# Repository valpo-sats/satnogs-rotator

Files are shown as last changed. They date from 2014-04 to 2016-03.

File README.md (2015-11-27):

# SatNOGS Rotator

Hardware for SatNOGS Rotator. This repository includes all needed source files for 3D printed (and other) parts of SatNOGS Rotator.

## Documentation

More information can be found in our [documentation](http://satnogs.org/documentation/hardware/), or our [wiki](https://wiki.satnogs.org).

## Repository policy
SatNOGS hardware repositories only track source design files. All needed derivative files (e.g. stl, grb etc) for production are created per release, packaged in an archive and uploaded linked to a  [release](https://github.com/satnogs/satnogs-rotator/releases).

Each major release (x.0.0) is branched out of master. Subsequent fixes (minor or not) are commited on those branches and tagged accordingly.

Master branch is most times under active development, so expect things to break. For production ready and previous releases source files check tags and branches.

## License

&copy; 2014-2015 [Libre Space Foundation](http://librespacefoundation.org).

Licensed under the [CERN OHLv1.2](LICENSE).

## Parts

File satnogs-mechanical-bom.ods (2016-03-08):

Part | Description | Distributor | Qty | Price Per Unit Small QNT (euro) | Total Price | Printing Time (min) | Price Per Unit Large QNT (euro) | Total price | Comments
axis_side.stl | Axis side, 3D printed | - | 2 | 0.8 | 1.6 | 110 | 0.8 | 1.6
axis_side_sensor_holder.stl | Axis side with homing sensor, 3D printed | - | 2 | 0.8 | 1.6 | 128 | 0.8 | 1.6
ball_bearing_housing.stl | Ball bearing housing, 3D printed | - | 4 | 0.8 | 3.2 | 46 | 0.8 | 3.2
axis_spacer.stl | Axis spacer, 3D printed | - | 2 | 0.8 | 1.6 | 15 | 0.8 | 1.6
axis_spacer_collar.stl | Axis spacer collar, 3D printed | - | 2 | 0.8 | 1.6 | 26 | 0.8 | 1.6
axis_gear.stl | Axis gear (Worm wheel), 3D printed | - | 2 | 0.8 | 1.6 | 172 | 0.8 | 1.6
homing_ring.stl | Homing ring, 3D printed | - | 2 | 0.8 | 1.6 | 25 | 0.8 | 1.6
worm_gear.stl | Worm gear, 3D printed | - | 2 | 0.8 | 1.6 | 105 | 0.8 | 1.6
worm_mount.stl | Worm mount, 3D printed | - | 2 | 0.8 | 1.6 | 84 | 0.8 | 1.6 | Printing time is for worm_mount and worm_mount_mirror
worm_mount_mirror.stl | Worm mount mirror, 3D printed | - | 2 | 0.8 | 1.6 | 84 | 0.8 | 1.6
motor_mount_flange.stl | DC Motor mount flange, 3D printed | - | 2 | 0.8 | 1.6 | 21 | 0.8 | 1.6
motor_mount.fcstd | Motor mount | [2] (http://grobotronics.com/stepper-motor-mount-with-hardware.html) | 2 | 4.8 | 9.6 | - | 2.75 | 5.5
encoder_holder.stl | Encoder holder, 3D printed | - | 2 | 0.8 | 1.6 | 81 | 0.8 | 1.6 | Printing time is for 2 encoder_holder and 2 M3_TSlot20_nut
t_slot20_102.fcstd | T slot 20x20 L102 | [1] (http://www.motedis.com/shop/) | 18 | 0.51 | 9.18 | - | 0.3 | 5.4
t_slot20_160.fcstd | T slot 20x20 L160 | [1] (http://www.motedis.com/shop/) | 8 | 0.8 | 6.4 | - | 0.47 | 3.76
axis_pipe_40mm.fcstd | Aluminum pipe Φ40 L1m | - | 2 | 5 | 10 | - | 3 | 6
M3_TSlot20_nut.stl | M3 nut adapter for t slot, to mount encoder Holder, 3D printed | - | 2 | 0.8 | 1.6 | 81 | 0.8 | 1.6
e_box_pcb_mount.stl | PCB mount | - | 1 | 0.8 | 0.8 | 2 | 0.8 | 0.8
lower_bottom.pdf | Part for weather proof box, 1st sheet | - | 1 | 2 | 2 | - | 1.6 | 1.6
lower_side_axis_A.pdf | Part for weather proof box, 1st sheet | - | 1 | 2 | 2 | - | 1.6 | 1.6
lower_side_axis_B.pdf | Part for weather proof box, 2nd sheet | - | 1 | 2 | 2 | - | 1.6 | 1.6
lower_side_axis_x2.pdf | Part for weather proof box, 2nd sheet | - | 2 | 2 | 4 | - | 1.6 | 3.2
upper_side_axis_A.pdf | Part for weather proof box, 3rd sheet | - | 1 | 2 | 2 | - | 1.6 | 1.6
upper_side_axis_B.pdf | Part for weather proof box, 3rd sheet | - | 1 | 2 | 2 | - | 1.6 | 1.6
upper_side_axis_x2.pdf | Part for weather proof box, 4th sheet | - | 2 | 2 | 4 | - | 1.6 | 3.2
upper_top.pdf | Part for weather proof box, 4th sheet | - | 1 | 2 | 2 | - | 1.6 | 1.6
rain_cover_box.stl | Part for weather proof box, 3D printed | - | 2 | 0.8 | 1.6 |  | 0.8 | 1.6
rain_cover_tube.stl | Part for weather proof box, 3D printed | - | 2 | 0.8 | 1.6 |  | 0.8 | 1.6
rain_cover_positioning_pattern.pdf | Pattern to place in the box the Rain_cover_box parts | - | 1 | 0 | 0 | - | 0 | 0
Hidden Corner Connection slot 6 | for t slots | [1] (http://www.motedis.com/shop/) | 44 | 1.4 | 61.6 | - | 0.75 | 33
M5 Threaded Rod | for axis of worm gear, 2xL90mm | - | 2 | 1 | 2 | - | 1 | 2
M5 Hex Nuts | for axis of worm gear | - | 6 | 0.02 | 0.12 | - | 0.02 | 0.12
M5 Washers | for axis of worm gear, OD:10mm | - | 6 | 0.012 | 0.072 | - | 0.012 | 0.072
M4 Nuts slot 6 | for t slots, electronics box and cover box | [1] (http://www.motedis.com/shop/) | 37 | 0.4 | 14.8 | - | 0.18 | 6.66
M4 Head Cap Screw L10 | for t slots, electronics box and cover box | - | 32 | 0.04 | 1.28 | - | 0.04 | 1.28
M4 Head Cap Screw L20 | for ball bearing housing and motor mount | - | 20 | 0.06 | 1.2 | - | 0.06 | 1.2
M4 Hex Nuts | for ball bearing housing and worm gear | - | 20 | 0.014 | 0.28 | - | 0.014 | 0.28
M4 Washers | general, OD:10mm | - | 24 | 0.012 | 0.288 | - | 0.012 | 0.288
M3 Hex Nuts | general | - | 32 | 0.012 | 0.384 | - | 0.012 | 0.384
M3 Washers | general, OD: 8mm | - | 26 | 0.012 | 0.312 | - | 0.012 | 0.312
M3 Set Screw L10 | for axis spacer collar | - | 12 | 0.04 | 0.48 | - | 0.04 | 0.48
M3 Head Cap Screw L6 | for stepper motor, DC motor mount flange ,Encoder holder and electronics box | - | 20 | 0.03 | 0.6 | - | 0.03 | 0.6
M3 Head Cap Screw L12 | for homing sensor holder and DC motor mount | - | 10 | 0.03 | 0.3 | - | 0.03 | 0.3
M3 Head Cap Screw L25 | for homing ring | - | 2 | 0.05 | 0.1 | - | 0.05 | 0.1
M2 Thread-Forming Screw L6 | for encoder holder | - | 2 | 0.05 | 0.1 | - | 0.05 | 0.1
Ball Bearing 6008ZZ | for main axis | - | 4 | 5 | 20 | - | 2 | 8
Ball Bearing 625ZZ | for worm gear axis | - | 4 | 0.8 | 3.2 | - | 0.45 | 1.8
Timing Pulley GT2, 6mm Belt, 20 Tooth, 6mm Bore |  | [2] (http://grobotronics.com/aluminum-gt2-timing-pulley-6mm-belt-20-tooth-5mm-bore.html) | 2 | 4 | 8 | - | 2.27 | 4.54 | For DC motor 6mm Bore
Timing Pulley GT2, 6mm Belt, 36 Tooth, 5mm Bore |  | [2] (http://grobotronics.com/aluminum-gt2-timing-pulley-6mm-belt-36-tooth-5mm-bore.html) | 2 | 6 | 12 | - | 3.4 | 6.8
Timing Belt GT2, 158mm, Wide 6mm | for both axis | [2] (http://grobotronics.com/timing-belt-gt2-158mm.html) | 2 | 1.5 | 3 | - | 0.85 | 1.7
 |  |  |  | Total | 211.696 |  |  | 133.076

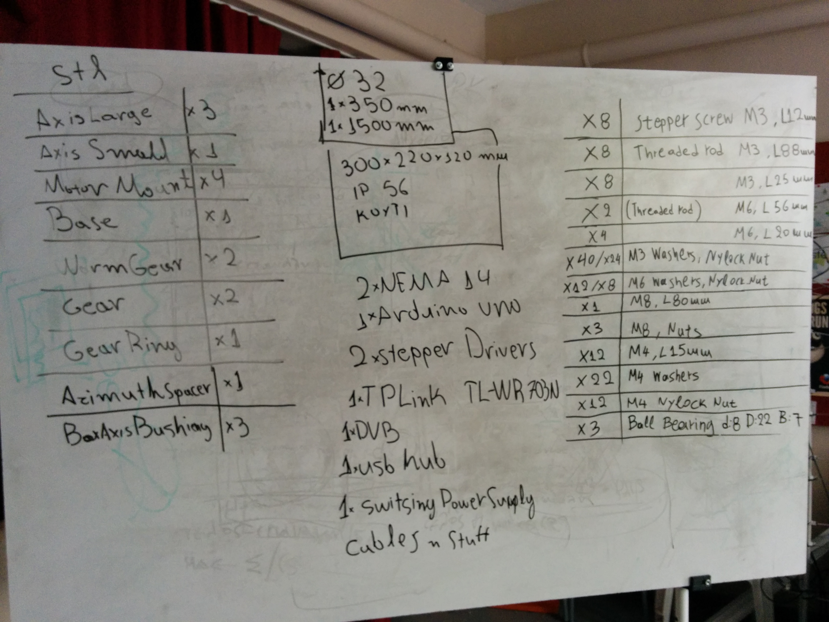
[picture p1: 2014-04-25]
doc/Parts.jpg

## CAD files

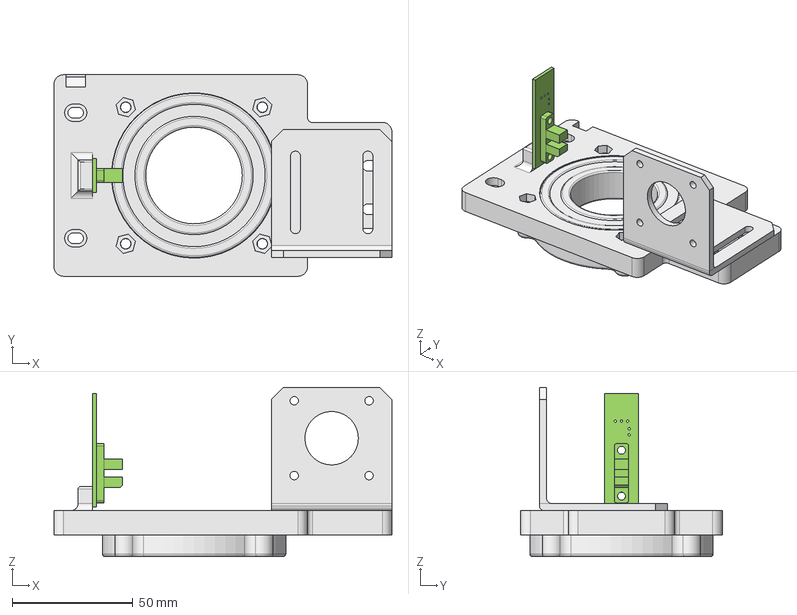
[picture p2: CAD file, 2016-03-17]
assemblies/axis_side_sensor_holder_assembly.fcstd
140.0 x 83.5 x 70.0 mm
axis_side_sensor_holder_01
satnogs_endstop_01
motor_mount_01
ball_bearing_housing_01
ball_bearing_6008ZZ_01

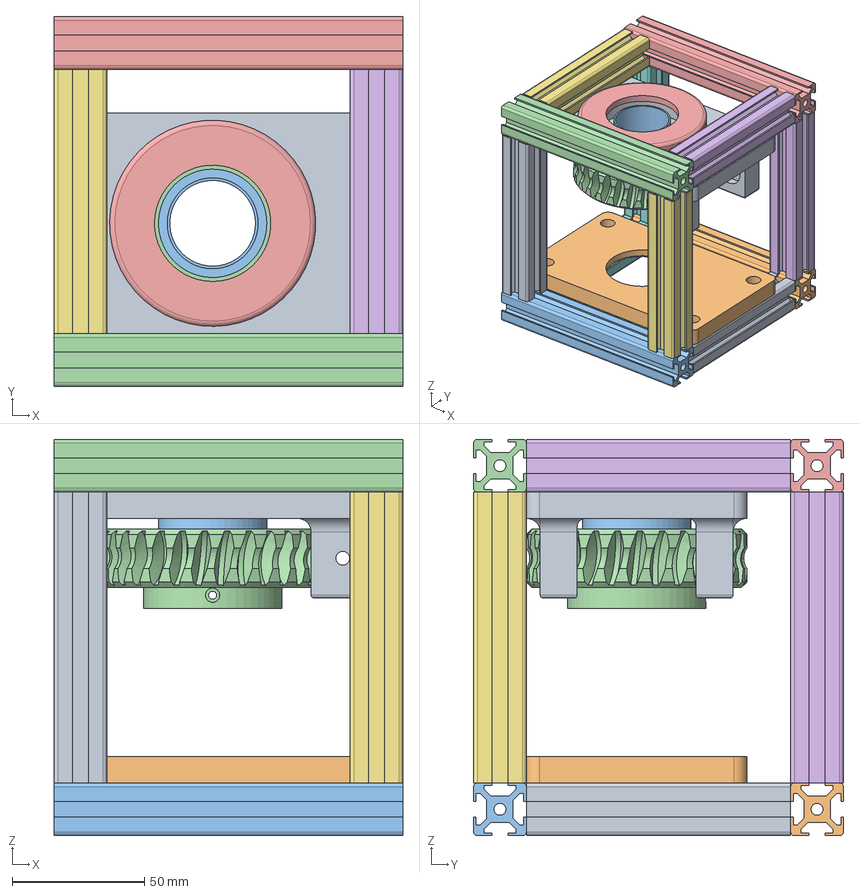
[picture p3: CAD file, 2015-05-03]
src/Assembly.fcstd
132.0 x 140.0 x 150.0 mm
axis_side_worm_mount_import01
axis_side_motor_mount_import01
axis_spacer_import01
axis_gear_import01
ball_bearing_housing_import01
t_slot20_100_import01
t_slot20_100_import02
t_slot20_100_import03
t_slot20_100_import04
t_slot20_132_import01
t_slot20_132_import02
t_slot20_132_import003
t_slot20_132_import004
t_slot20_110_import01
t_slot20_110_import002
t_slot20_110_import003
t_slot20_110_import004

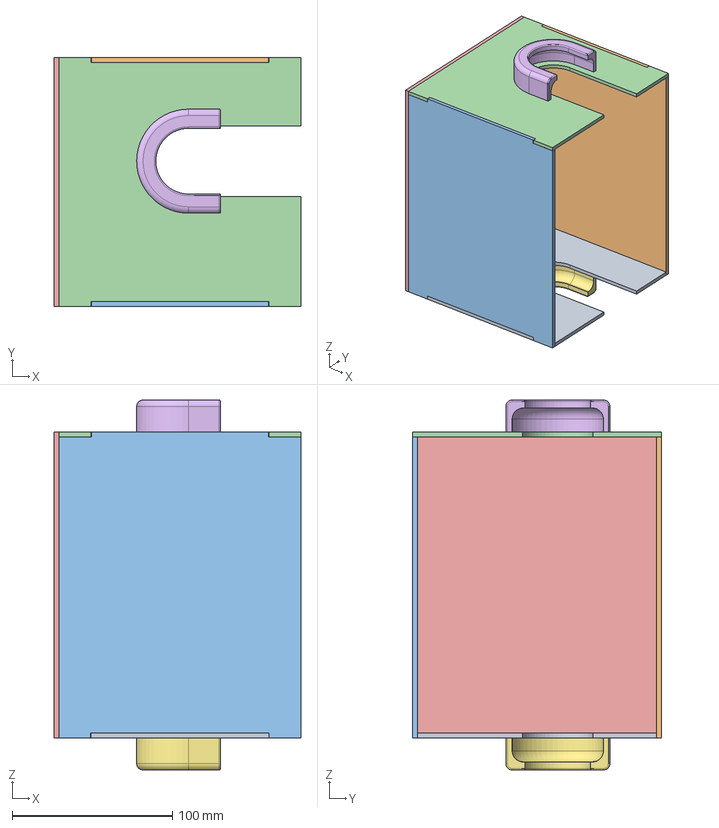
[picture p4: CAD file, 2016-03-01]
assemblies/cover_up_assembly.fcstd
154.0 x 155.5 x 231.0 mm
upper_side_axis_A_01
upper_side_axis_x2_01
upper_side_axis_x2_02
upper_side_axis_B_01
upper_top_01
rain_cover_box_01
rain_cover_box_02

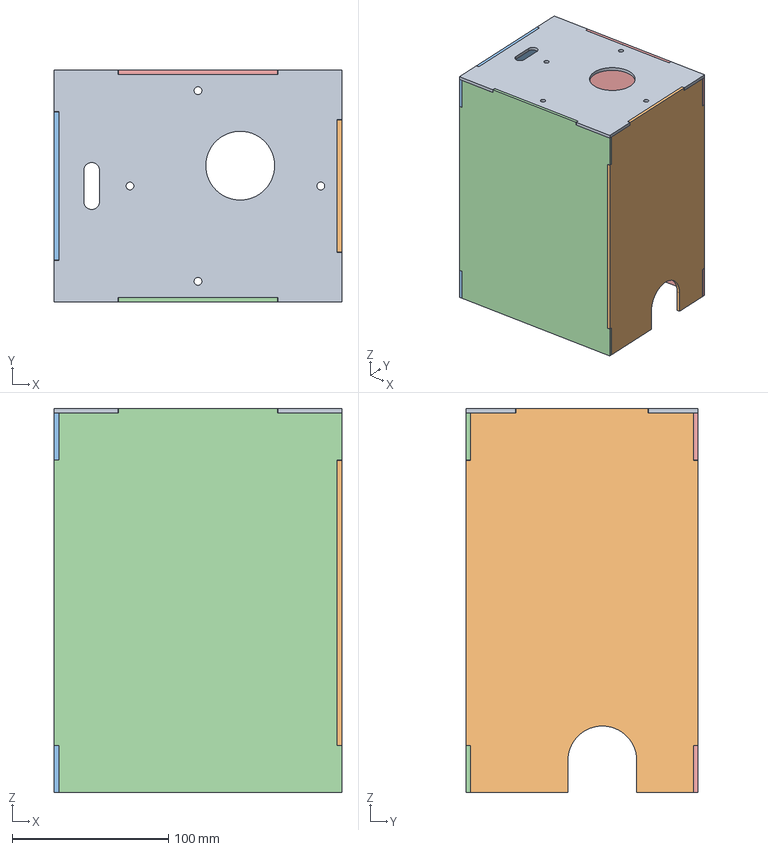
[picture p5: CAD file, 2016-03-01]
assemblies/cover_down_assembly.fcstd
184.0 x 148.5 x 245.5 mm
lower_bottom_01
lower_side_axis_A_01
lower_side_axis_B_01
lower_side_axis_x2_01
lower_side_axis_x2_02

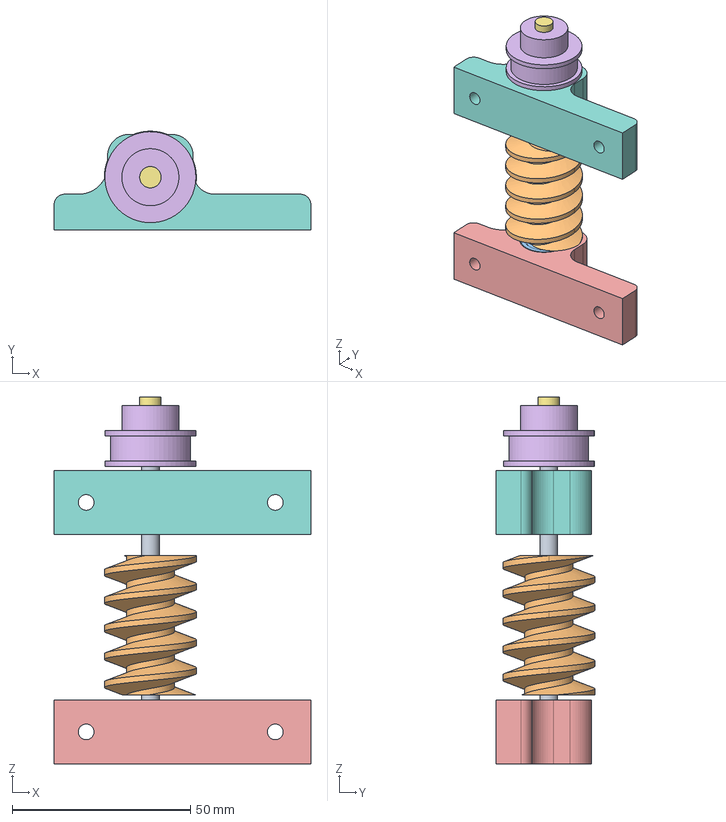
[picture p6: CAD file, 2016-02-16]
assemblies/worm_gear_assembly.fcstd
72.0 x 27.7 x 102.9 mm
worm_axis_01
worm_gear_01
ball_bearing_625ZZ_01
ball_bearing_625ZZ_02
worm_mount_01
timing_pulley_gt2_36T_01
encoder_magnet_01
worm_mount_mirror_01

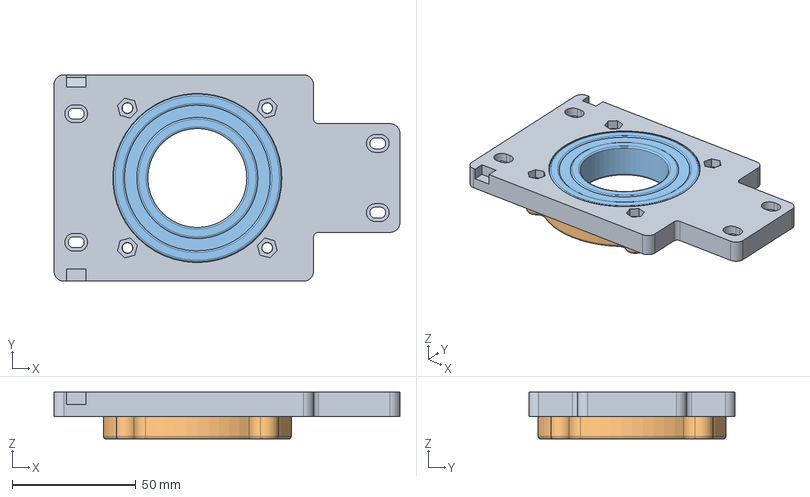
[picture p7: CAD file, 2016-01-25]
assemblies/axis_side_assembly.fcstd
140.0 x 83.5 x 19.0 mm
axis_side_01
ball_bearing_housing_01
ball_bearing_6008ZZ_01

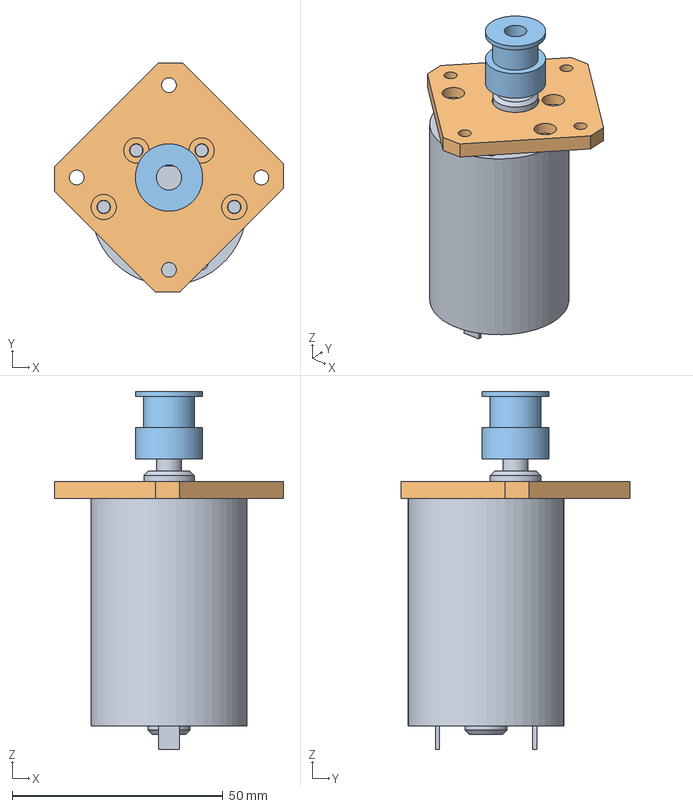
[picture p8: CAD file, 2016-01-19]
assemblies/dc_motor_assembly.fcstd
54.4 x 54.4 x 85.0 mm
dc_motor_50_1_01
motor_mount_flange_01
timing_pulley_gt2_20T_01

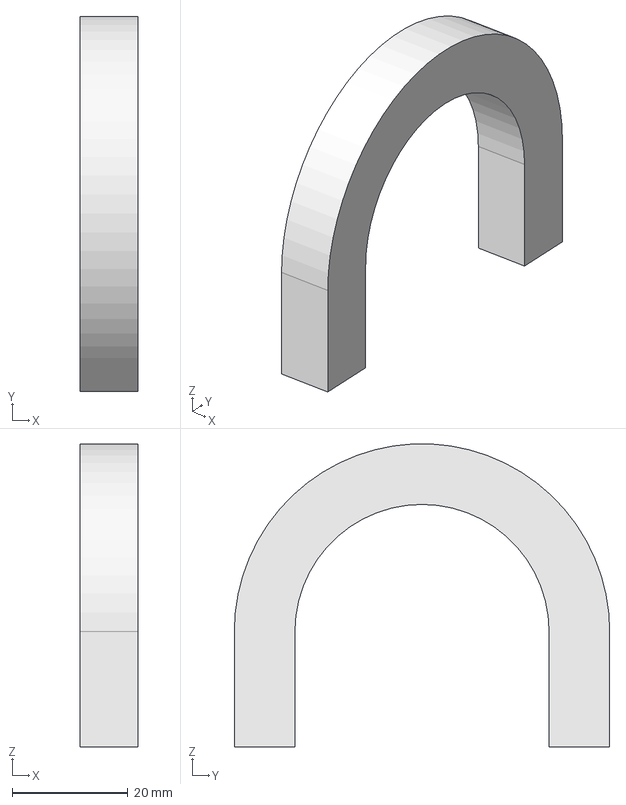
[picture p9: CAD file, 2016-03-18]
cover/rain_cover_positioning_pattern.fcstd
10.0 x 65.0 x 52.5 mm

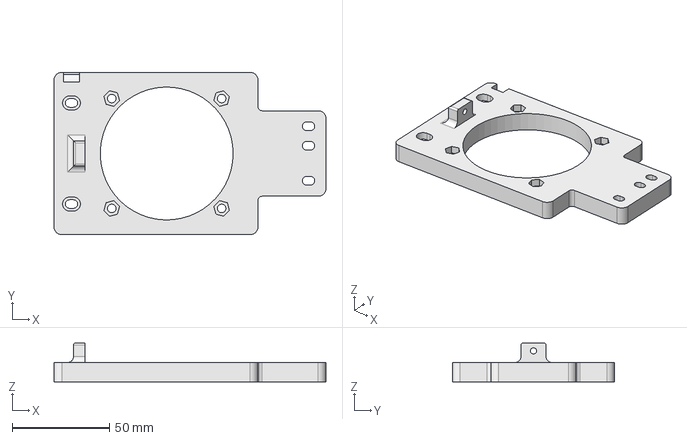
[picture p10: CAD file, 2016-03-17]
rotator_parts/axis_side_sensor_holder.fcstd
140.0 x 83.5 x 20.0 mm

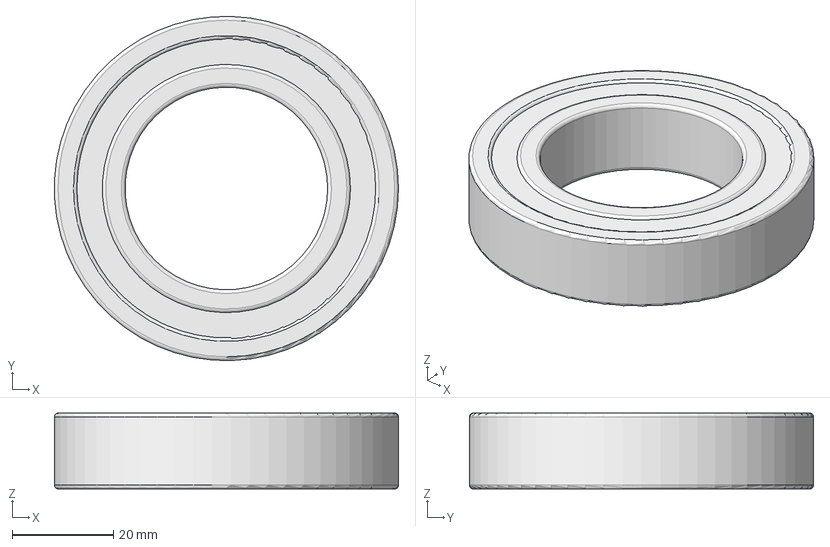
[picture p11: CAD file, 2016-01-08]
shared/ball_bearing_6008ZZ.fcstd
67.9 x 68.0 x 15.0 mm

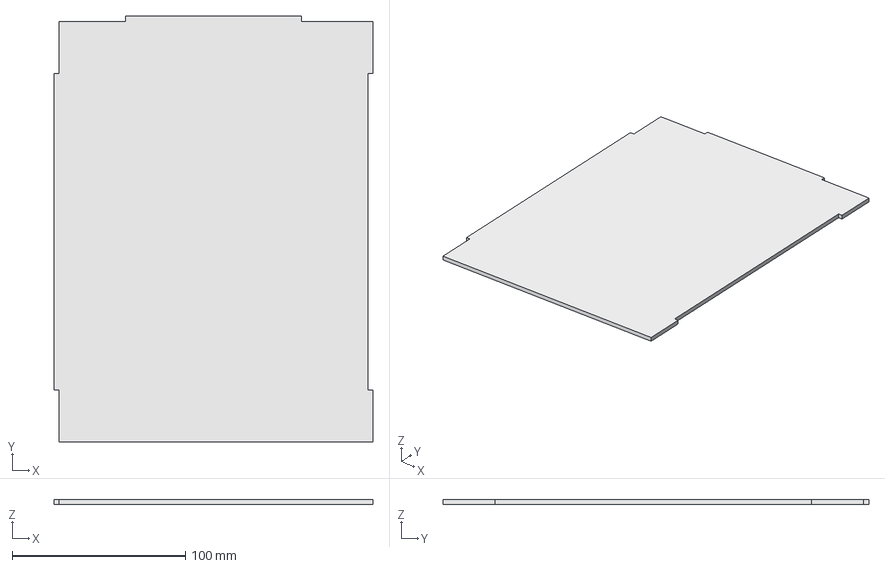
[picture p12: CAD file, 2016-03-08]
cover/lower_side_axis_x2.fcstd
184.0 x 245.5 x 3.00 mm

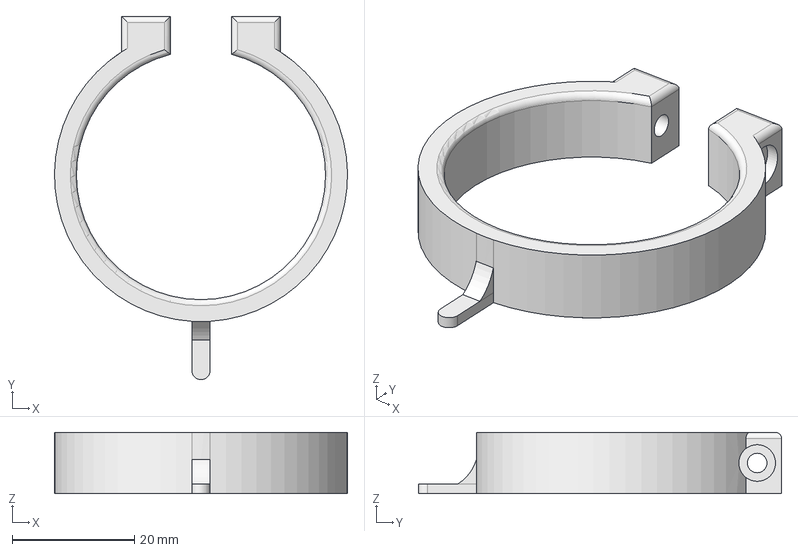
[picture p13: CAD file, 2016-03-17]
rotator_parts/homing_ring.fcstd
48.0 x 59.5 x 10.0 mm

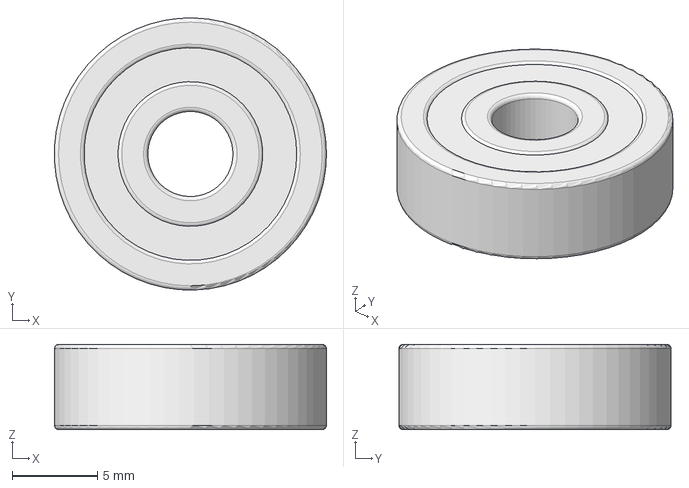
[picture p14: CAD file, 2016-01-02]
shared/ball_bearing_625ZZ.fcstd
16.0 x 16.0 x 5.00 mm

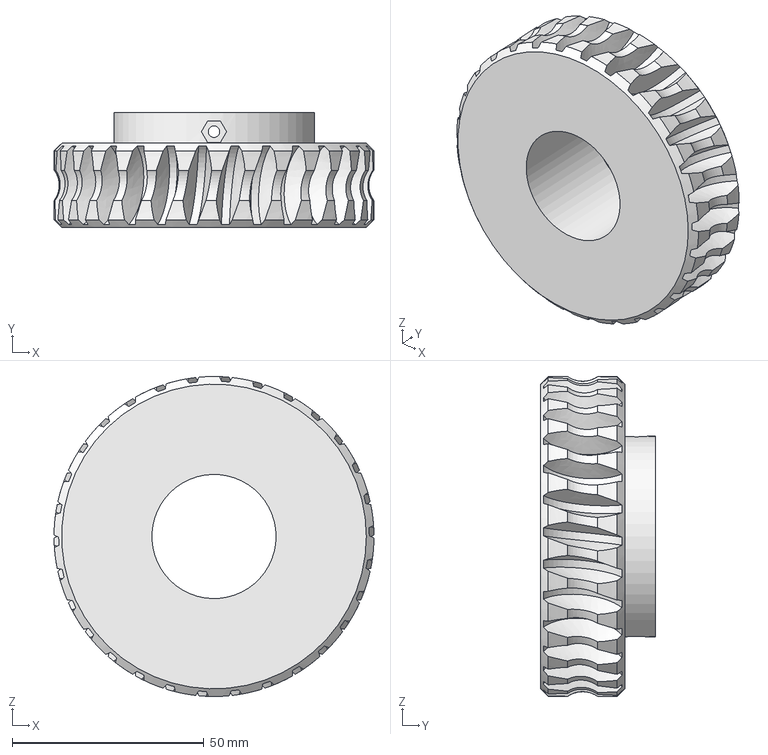
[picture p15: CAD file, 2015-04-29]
src/axis_gear.fcstd
83.5 x 30.0 x 83.5 mm

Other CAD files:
cover/upper_side_axis_x2.fcstd
rotator_parts/axis_pipe_40mm.fcstd
shared/dc_motor_50:1.fcstd
assemblies/electronics_box.fcstd
assemblies/frame.fcstd
cover/lower_bottom.fcstd
cover/lower_side_axis_A.fcstd
cover/lower_side_axis_B.fcstd
cover/rain_cover_box.fcstd
cover/rain_cover_tube.fcstd
cover/upper_side_axis_A.fcstd
cover/upper_side_axis_B.fcstd
cover/upper_top.fcstd
rotator_parts/M3_TSlot20_Nut.fcstd
rotator_parts/axis_pipe_32mm.fcstd
rotator_parts/axis_side.fcstd
rotator_parts/axis_spacer.fcstd
rotator_parts/axis_spacer_collar.fcstd
rotator_parts/ball_bearing_housing.fcstd
rotator_parts/e_box_bottom.fcstd
rotator_parts/e_box_pcb_mount.fcstd
rotator_parts/e_box_top.fcstd
rotator_parts/encoder_holder.fcstd
rotator_parts/encoder_magnet.fcstd
rotator_parts/motor_mount_flange.fcstd
rotator_parts/pcb_mount.fcstd
rotator_parts/satnogs_encoder.fcstd
rotator_parts/satnogs_endstop.fcstd
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

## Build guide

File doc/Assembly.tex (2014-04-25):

\documentclass[a4paper]{article}

\usepackage[english]{babel}
\usepackage{fancyhdr}
\usepackage{array}
\usepackage{caption}
\usepackage{subcaption}
\usepackage{graphicx}                 

\pagestyle{fancy}

\fancyhf{}
\fancyfoot[C] {
	\vspace{1pt}
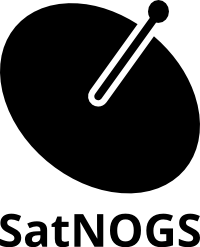
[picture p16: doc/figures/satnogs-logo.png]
	
}

\begin{document}

\begin{center}
	\begin{tabular}{ | l | l | l | l |}
	\hline
 	\multicolumn{3}{|c|}{Embedded Systems} \\
 	\hline
	Part & Qty & Description \\ \hline
	NEMA14& 2 & Stepper Motor \\ \hline
	Arduino UNO & 1 & Microcontroller \\ \hline
	Stepper Motor Drivers & 2 & \\ \hline
 	TP-Link TL-WR703N & 1 & Single-board computer \\ \hline
	DVB & 1 & Signal receiver \\ \hline
	USB Hub & 1 & ---\\ \hline
	Switching Power Supply & 1 & specs\\ \hline
	Cables & --- & ---\\ \hline
    	\end{tabular}
\end{center}

\vspace{0.5cm}

\begin{center}
	\begin{tabular}{ | l | l | l | l |}
	\hline
 	\multicolumn{3}{|c|}{3D printing Parts} \\
 	\hline
	Part & Qty & Description \\ \hline
	axis large.stl & 3 & \\ \hline
	axis small.stl & 1 & \\ \hline
	motor mount.stl & 4 & \\ \hline
 	base.stl & 1 & \\ \hline
	worm gear.stl & 2 &\\ \hline
	gear.stl & 2 &\\ \hline
	gear ring.stl & 1 &\\ \hline
	azimuth spacer.stl & 1 &\\ \hline
	box axis bushing.stl & 3 &\\ \hline
 	\multicolumn{3}{|c|}{Other Parts} \\
 	\hline
	Φ32,L350 PVC Tube & 1 & Azimuth axis\\ \hline
	Φ32,L1500 PVC Tube & 1 & Altitude axis\\ \hline
	IP56 Box 300x220x120 & 1 & The box host all the system\\ \hline
    	\end{tabular}
\end{center}

\vspace{0.5cm}

\begin{center}
	\begin{tabular}{ | l | l | l | l |}
	\hline
 	\multicolumn{3}{|c|}{Fasteneres} \\
 	\hline
	Part & Qty & Description \\ \hline
	M3,L12 Allen Cap Screw & 8 & For stepper motors \\ \hline
	M3,L88 Threaded Rod & 8 & For motor base \\ \hline
	M3,L25 Allen Cap Screw & 8 & For connection of main base with motor base \\ \hline
 	M6,L56 Threaded Rod & 2 & For connection of the gear with axis \\ \hline
	M6,L20 Hex Cap Screw & 4 & For connection of the main base with the box \\ \hline
	M3 Washers & 40 & --- \\ \hline
	M3 Nylock Nuts & 24 & --- \\ \hline
	M6 Washers & 12 & --- \\ \hline
	M6 Nylock Nuts & 8 & --- \\ \hline
	M8,L80 Hex Cap Screw & 1 & For Azimuth axis \\ \hline
	M8 Nuts & 3 & For Azimuth axis \\ \hline
	M4,L15 Allen Cap Screw & 12 & Used to connect bushing to the waterproof box \\ \hline
	M4 Washers & 22 & --- \\ \hline
	M4 Nylock Nuts & 12 & --- \\ \hline
	Ball Bearings d:8 D:22 B:7 & 3 & For stepper axis and Azimuth axis\\ \hline
    	\end{tabular}
\end{center}

\newpage

\begin{figure}
       \centering
        \begin{subfigure}[b]{0.3\textwidth}
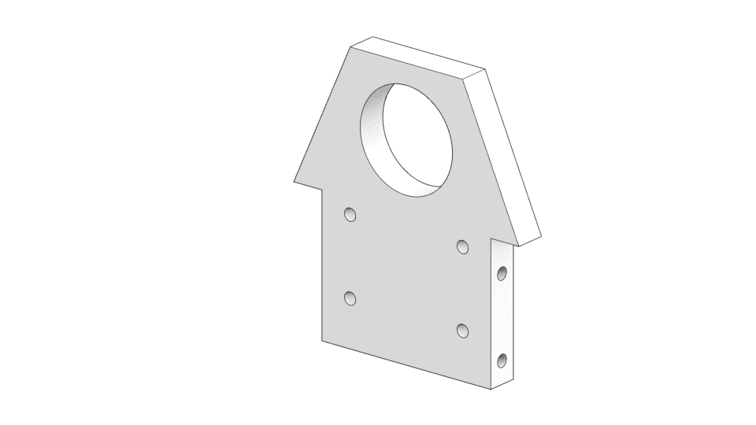
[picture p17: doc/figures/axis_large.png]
                
                \caption*{axis large.stl }
        \end{subfigure}
        ~ 
        \begin{subfigure}[b]{0.3\textwidth}
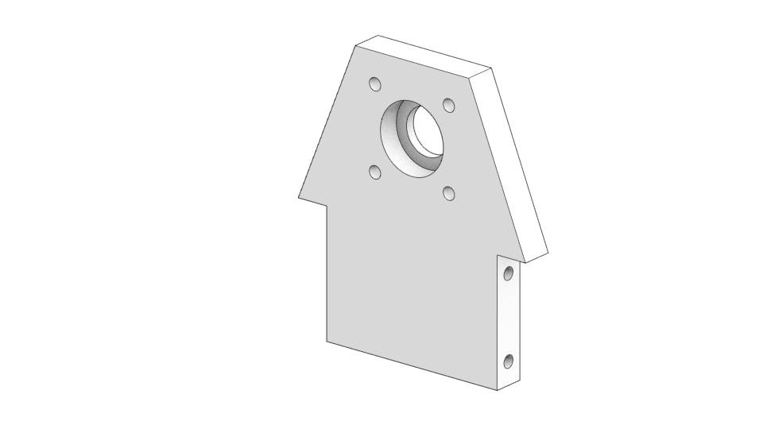
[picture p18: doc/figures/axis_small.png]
                
                \caption*{axis small.stl }
        \end{subfigure}
        ~ 
        \begin{subfigure}[b]{0.3\textwidth}
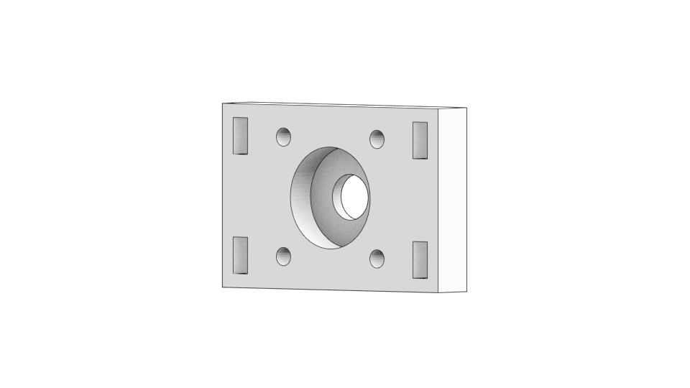
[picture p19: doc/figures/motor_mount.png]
                
                \caption*{motor mount.stl }
        \end{subfigure}
\end{figure}

\vspace{0.5cm}

\begin{figure}
        \centering
        \begin{subfigure}[b]{0.3\textwidth}
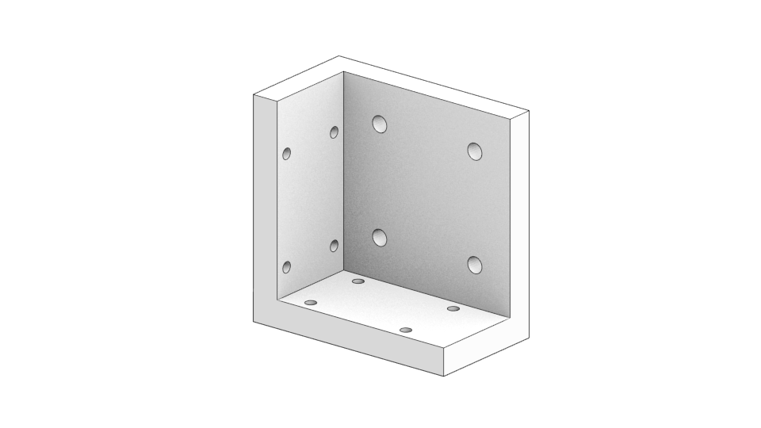
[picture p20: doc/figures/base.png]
                
                \caption*{base.stl }
        \end{subfigure}
        ~ 
        \begin{subfigure}[b]{0.3\textwidth}
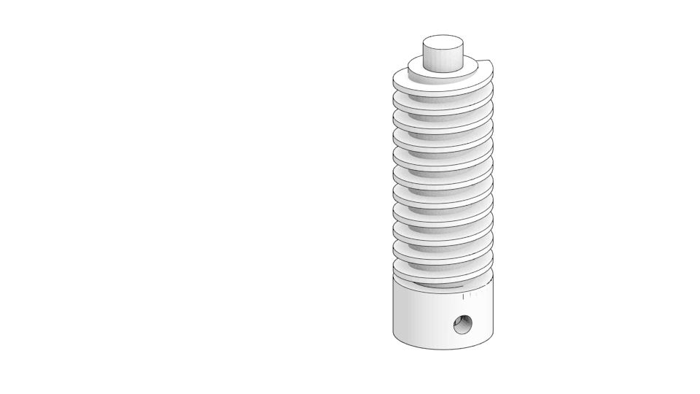
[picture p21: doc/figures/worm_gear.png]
                
                \caption*{worm gear.stl }
        \end{subfigure}
        ~ 
        \begin{subfigure}[b]{0.3\textwidth}
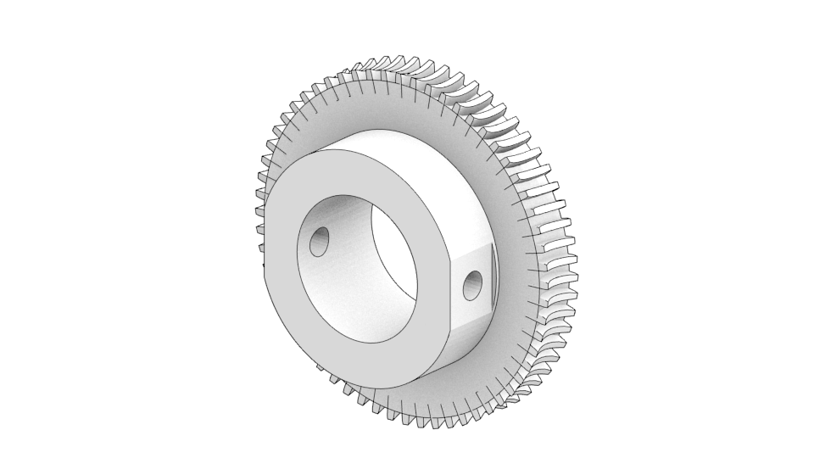
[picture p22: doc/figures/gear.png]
                
                \caption*{gear.stl }
        \end{subfigure}
\end{figure}

\vspace{0.5cm}

\begin{figure}
        \centering
        \begin{subfigure}[b]{0.3\textwidth}
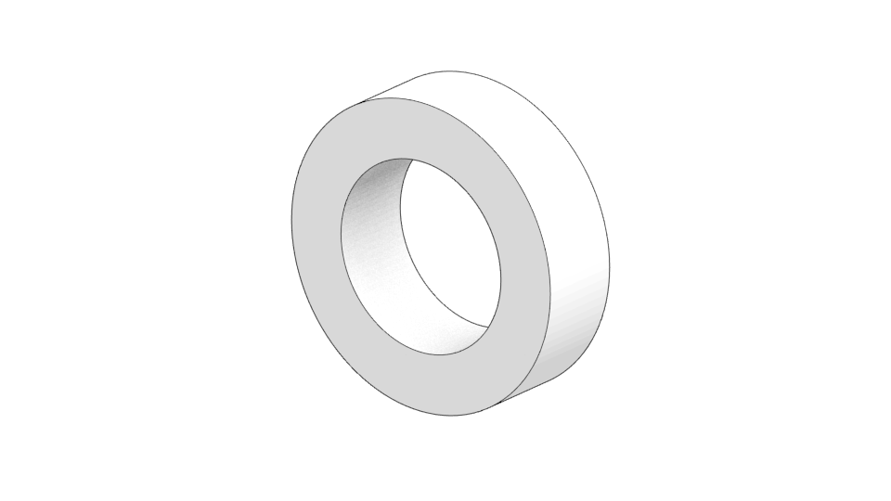
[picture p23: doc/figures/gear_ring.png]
                
                \caption*{gear ring.stl }
        \end{subfigure}
        ~ 
        \begin{subfigure}[b]{0.3\textwidth}
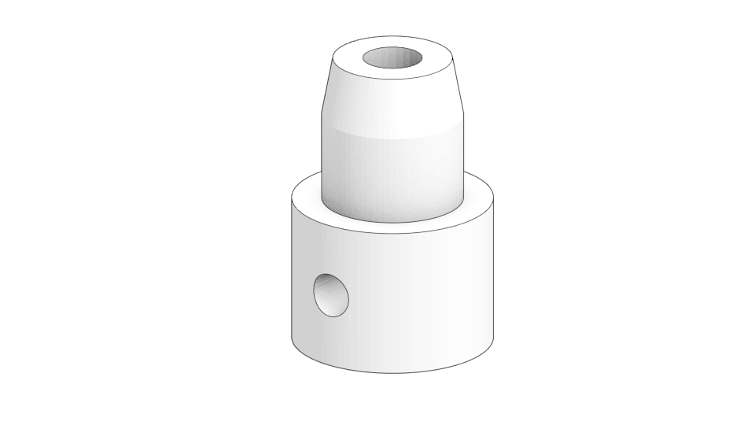
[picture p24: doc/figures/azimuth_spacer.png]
                
                \caption*{azimuth spacer.stl }
        \end{subfigure}
        ~ 
        \begin{subfigure}[b]{0.3\textwidth}
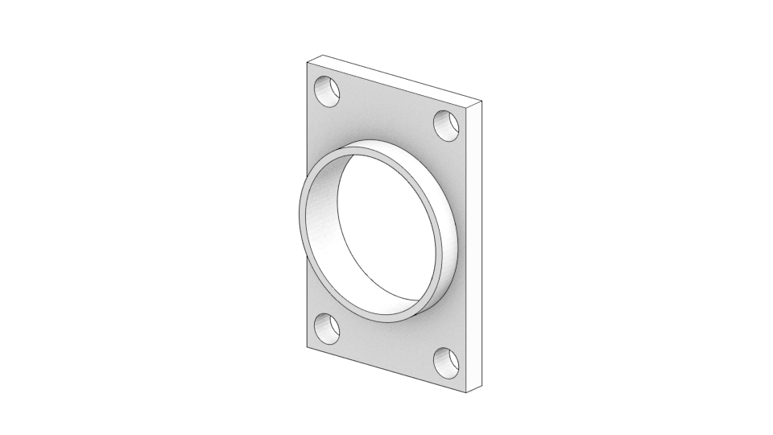
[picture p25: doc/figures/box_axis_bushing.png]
                
                \caption*{box axis bushing.stl }
        \end{subfigure}
\end{figure}

\vspace{0.5cm}

\begin{figure}
        \centering
        \begin{subfigure}[b]{0.3\textwidth}
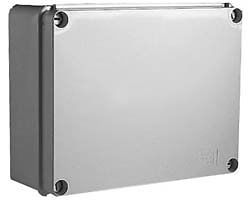
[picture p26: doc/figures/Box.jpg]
                
                \caption*{IP56 Box 300x220x120 }
        \end{subfigure}
\end{figure}

\end{document}

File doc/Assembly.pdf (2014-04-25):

Embedded Systems
Part | Qty | Description
NEMA14 | 2 | Stepper Motor
Arduino UNO | 1 | Microcontroller
Stepper Motor Drivers | 2
TP-Link TL-WR703N | 1 | Single-board computer
DVB | 1 | Signal receiver
USB Hub | 1 | —
Switching Power Supply | 1 | specs
Cables | — | —

3D printing Parts
Part | Qty | Description
axis large.stl | 3
axis small.stl | 1
motor mount.stl | 4
base.stl | 1
worm gear.stl | 2
gear.stl | 2
gear ring.stl | 1
azimuth spacer.stl | 1
box axis bushing.stl | 3
Other Parts
32,L350 PVC Tube | 1 | Azimuth axis
32,L1500 PVC Tube | 1 | Altitude axis
IP56 Box 300x220x120 | 1 | The box host all the system

Fasteneres
Part | Qty | Description
M3,L12 Allen Cap Screw | 8 | For stepper motors
M3,L88 Threaded Rod | 8 | For motor base
M3,L25 Allen Cap Screw | 8 | For connection of main base with motor base
M6,L56 Threaded Rod | 2 | For connection of the gear with axis
M6,L20 Hex Cap Screw | 4 | For connection of the main base with the box
M3 Washers | 40 | —
M3 Nylock Nuts | 24 | —
M6 Washers | 12 | —
M6 Nylock Nuts | 8 | —
M8,L80 Hex Cap Screw | 1 | For Azimuth axis
M8 Nuts | 3 | For Azimuth axis
M4,L15 Allen Cap Screw | 12 | Used to connect bushing to the waterproof box
M4 Washers | 22 | —
M4 Nylock Nuts | 12 | —
Ball Bearings d:8 D:22 B:7 | 3 | For stepper axis and Azimuth axis

axis large.stl | axis small.stl | motor mount.stl
base.stl | worm gear.stl | gear.stl
gear ring.stl | azimuth spacer.stl | box axis bushing.stl


IP56 Box 300x220x120

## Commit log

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2015-04-16 Add versioin 3 source and stl files
    [Assembly.fcstd, axis_side_motor_mount.fcstd, axis_side_motor_mount.stl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]
2015-04-29 Add axis gear source and stl files updated for the version 3.
    [axis_gear.fcstd, axis_gear.stl]
2015-04-29 Add source and stl files for the new worm gear design.
    [worm_gear.fcstd, worm_gear.stl]
2015-05-03 Update axis_side_worm_mount part. *Change the dimensions for new worm gear. *Add M5 holes in order to mount to T slots.
    [axis_side_worm_mount.fcstd, axis_side_worm_mount.stl]
2015-05-03 Update axis_side_motor_mount part. *Change dimensions for motor mount. *Add M5 holes in order to mount T slots.
    [axis_side_motor_mount.fcstd, axis_side_motor_mount.stl]
2015-05-03 Change the dimensions of ball_bearing_housing part.
    [ball_bearing_housing.fcstd, ball_bearing_housing.stl]
2015-05-03 Add new part axis_spacer. *Convert D32mm of axis to D35 of ball bearing.
    [axis_spacer.fcstd, axis_spacer.stl]
2015-05-03 Update Assembly with new parts.
    [Assembly.fcstd]
2015-05-05 Add motor mount part source and stl.
    [worm_mount.fcstd, worm_mount.stl]
2015-05-05 Repair worm mount part.
    [worm_mount.fcstd, worm_mount.stl]
2015-05-05 Quick fix for worm_mount part.
    [worm_mount.fcstd, worm_mount.stl]
2015-05-05 Add mounting holes in ball bearing housing part.
    [ball_bearing_housing.fcstd, ball_bearing_housing.stl]
2015-05-06 Add last changes to worm gear part.
    [worm_gear.fcstd, worm_gear.stl]
2015-05-06 Add axis spacer colar source and .stl files.
    [axis_spacer_colar.fcstd, axis_spacer_colar.stl]
2015-05-06 Fix typo in axis spacer collar file name.
    [axis_spacer_collar.fcstd, axis_spacer_collar.stl]
2015-05-06 Change the diameter to feet better in the ball bearing.
    [axis_spacer.fcstd, axis_spacer.stl]
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2015-05-06 Change the diameter in the hole for axis, to solve friction problem.
    [worm_mount.fcstd, worm_mount.stl]
2015-05-12 Fixes in motor mount, axis spacer collar and worm mount parts.
    [axis_spacer_collar.fcstd, axis_spacer_collar.stl, motor_Mount.fcstd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]
2015-05-12 Fixes in axis_side and axis_spacer.
    [axis_side.fcstd, axis_side.stl, axis_spacer.fcstd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]
2015-06-02 Add latest changes to motor mount, homing ring and homing sensor holder.
    [homing_ring.fcstd, homing_ring.stl, homing_sensor_holder.fcstd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]
2015-06-14 Add to axis side the base of homing sensor.
    [axis_side_sensor_holder.fcstd, axis_side_sensor_holder.stl, homing_sensor_holder.fcstd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]
2015-06-14 Small fixes and update assembly.
    [axis_side.fcstd, axis_side.stl, axis_spacer_collar.fcstd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]
2015-06-14 Add correct stl files.
    [axis_side_sensor_holder.stl, homing_ring.stl, worm_mount.stl]
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2015-06-18 Fix the qty of t slots L102 in BOM.
    [satnogs-mechanical-bom.ods]
2015-07-14 Repair a misaligned hole in motor mount part.
    [motor_Mount.fcstd, motor_mount.stl]
2015-07-22 Fixes in motor mount part and update the assembly file.
    [motor_Mount.fcstd, motor_mount.stl]
2015-08-06 Add t slot 20 connectors src and stl.
    [t_slot20_connector.fcstd, t_slot20_connector.stl]
2015-08-06 Fixes in BOM.
    [satnogs-mechanical-bom.ods]
2015-08-12 Adding imperial v3 rotator parts
    Attaching 4 parts that are resized for imperial PVC sizes. I am
    just merging the .stl files, leaving the changes to source out of
    this as we do not want to manually keep up with parallel tracks
    of source files as the desire is to make them configurable in the
    future. If the source for these imperial changes is needed, it
    can be found at
    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
    [axis_gear_imperial.stl, axis_spacer_collar_imperial.stl, axis_spacer_imperial.stl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]
2015-09-07 Updates for axis gear, t-slot20 connector parts and assembly file.
    Add a different way to mount axis gear.
    Change t-slot20 connector for use with two M5 screws.
    [axis_gear.stl, t_slot20_connector.fcstd, t_slot20_connector.stl]
2015-09-16 Add source and .stl files for v3 rain covers.
    [rain_cover_box.fcstd, rain_cover_box.stl, rain_cover_tube.fcstd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]
2015-09-18 Add the files for the cover and some helping parts. The files for the cover are supposed to be cut on a laser cutter on 5mm acrylic (or similar material). Add a pattern to help align the rain cover p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
    [M3_TSlot20_Nut.fcstd, M3_TSlot20_nut.stl, lower_bottom.fcstd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]
2015-09-18 Fix a dimention problem in the lower bottom part.
    [lower_bottom.fcstd]
2015-09-18 Fix a dimention problem in the lower side x2 part.
    [lower_side_axis_x2.fcstd]
2015-09-20 Add the cover assembly file and the source file for the encoder holder part.
    [assembly.fcstd, encoder_holder.fcstd]
2015-09-29 Add missing worm_mount_mirror.stl file
    The worm_mount_mirror.stl file is missing from the repository
    Exported from the fcstd in /src/
    [worm_mount_mirror.stl]
2015-10-27 Update encoder mount and assembly.
    [encoder_holder.fcstd]
2015-10-27 Add DC motor mount flange. This part is an adapter, to use the stepper motor mount with DC motor.
    [motor_mount_flange.fcstd, motor_mount_flange.stl]
2015-11-10 Update cover box. Change the thickness to 1mm. Small fixes.
    [assembly.fcstd, lower_bottom.fcstd, lower_side_axis_A.fcstd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]
2015-11-14 Update and add parts for encoder and DC motor.
    [axis_side_sensor_holder.fcstd, encoder_holder.fcstd, encoder_magnet.fcstd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]
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2015-11-27 Update files because of new repository policy.
    [M3_TSlot20_Nut.fcstd, M3_TSlot20_nut.stl, axis_gear.stl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]
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2016-01-02 Add new parts for rotator assembly, add AZ EL rotator.
    [axis_pipe.fcstd, ball_bearing_6007ZZ.fcstd, ball_bearing_625ZZ.fcstd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]
2016-01-08 Change axis pipe to OD 40mm and update all parts and BOM. Rotator assembly is in progress.
    [axis_pipe.fcstd, axis_pipe_32mm.fcstd, axis_pipe_40mm.fcstd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]
2016-01-19 Reodrer the file structure and update parts. Update ball_bearing_housing.
    [M3_TSlot20_Nut.fcstd, axis_pipe_32mm.fcstd, axis_pipe_40mm.fcstd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]
2016-01-25 Add prises in the bulk order list in BOM.
    [satnogs-mechanical-bom.ods]
2016-01-25 Change bolts to M4, update axis gear, assemblies and BOM.
    [axis_side.fcstd, axis_side_assembly.fcstd, axis_side_sensor_holder.fcstd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]
2016-02-16 Update cover box and assembly. Change the thickness of sheets to 3mm. Add tolerances to parts. Change parts dimensions for 40mm axis pipe.
    [cover_assembly.fcstd, cover_down_assembly.fcstd, cover_up_assembly.fcstd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]
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2016-03-01 Update the cover_box. Increase tolerance in upper_side parts.
    [cover_down_assembly.fcstd, cover_up_assembly.fcstd, lower_bottom.fcstd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]
2016-03-01 Update Az El rotator assembly and BOM. Increase the axis pipe to 320mm. Connect rotator assemblies in different configuration. Add new prices and qty in BOM.
    [axis_pipe_40mm.fcstd, satnogs-mechanical-bom.ods]
2016-03-08 Add annotate page in cover parts and update BOM.
    [lower_bottom.fcstd, lower_side_axis_A.fcstd, lower_side_axis_B.fcstd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]
2016-03-17 Resolve collision between homing ring and sensor.
    [homing_ring.fcstd]
2016-03-17 Resolve problem in axis side sensor holder. Add pocket in M3 screw for homing sensor.
    [axis_side_sensor_holder.fcstd, axis_side_sensor_holder_assembly.fcstd]
2016-03-18 Update rain cover positioning pattern for new mast.
    [rain_cover_positioning_pattern.fcstd]
